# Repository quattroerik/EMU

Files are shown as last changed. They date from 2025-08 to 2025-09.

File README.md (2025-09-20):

[][cc-by-nc-sa]

# EMU – Expandable Multi-material Unit
### A new take on a MMU by <a href="https://github.com/DW-Tas">DW-Tas</a> and <a href="https://github.com/igiannakas">igiannakas</a><br/>
<a href="https://ko-fi.com/O5O5OCC0K"> Ko-Fi</a>

> [!WARNING] 
> ***Under Active/Early Development*** <br/>
> Build at your own risk

**Introducing the EMU, the Expandable Multi-material Unit from down under.** The EMU is a modular, flexible, upgradable, reliable and service-friendly MMU designed around the proven filamentalist V3 platform.

The EMU supports any number of lanes and base configurations; whether it is a **single lane setup** to assist filament loading, a **dual lane configuration** for endless spool, or a **multi-lane, multi base unit setup** for multi-material printing. It is also **expandable**, with no re-printing of parts required when upgrading from a 2 lane to a multiple lane setup.

<p align="center">
  
</p>

#### Table of Contents
- [Design Objectives & Key Features](#design-objectives)
- [BOM](#bom)
- [Assembly Videos](#assembly-videos)
- [Wiring Instructions and Diagrams](#wiring-diagrams)
- [Render Gallery](#render-gallery)
- [License](#this-work-is-licensed-under-a)

#### Highlights:
- **Modular & Expandable** design, able to add lanes anytime and in any configuration. No reprints when upgrading from a 2 lane setup.
- **One screw or tool-free** access and servicing, even mid-print.
- **Sealed dry boxes** able to maintain humidity in the 15% range (with silica gel) or 5–8% range (with molecular sieves) for weeks.  
- **Humidity** sensors per lane for environmental monitoring.
- **Reliable endless spool** with no chance of the rewound filament interfering with neighbouring rolls.
- **Off-the-shelf electronics** (EBB42 with EBB36 also fully compatible).  
- **Per-lane controls** - eject button + LEDs.

<p align="center">
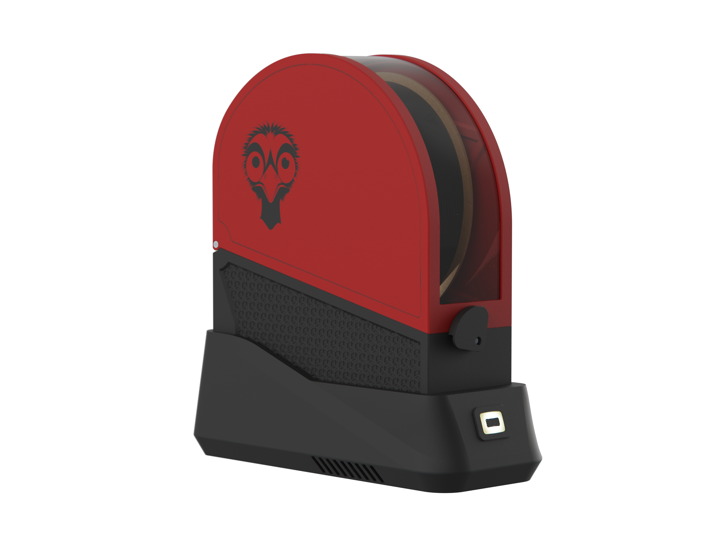
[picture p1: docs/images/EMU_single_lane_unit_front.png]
  
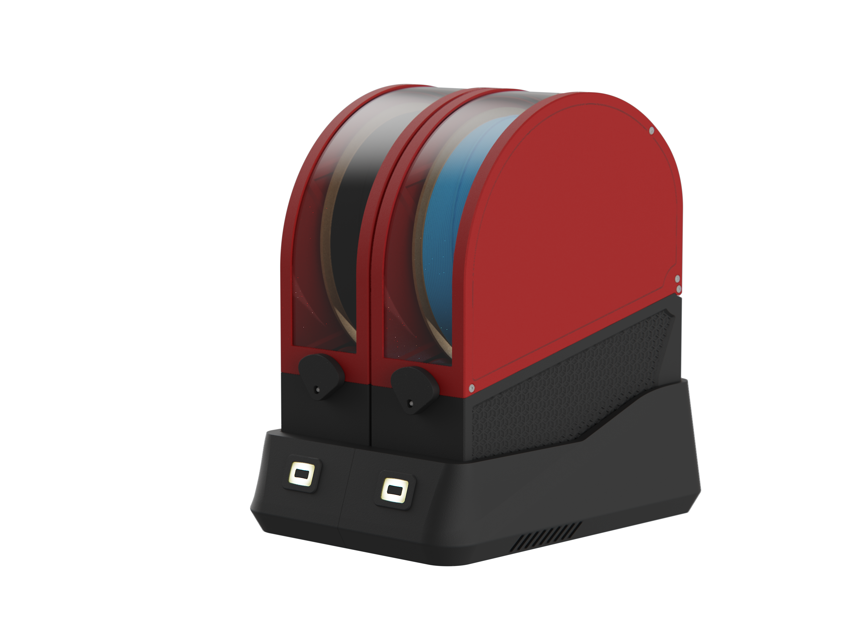
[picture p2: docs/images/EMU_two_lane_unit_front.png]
  
</p>

## Design Objectives

#### Modularity & Upgradeability  
Each lane is fully self-contained, so you can choose **exactly how many lanes you need and group them as you like**. You can also **mix and match** lanes across multiple base units, or use a stand-alone single lane for extruder loading and print assistance. 

Expanding later is also straightforward. Just print lane expanders for the base and add another dry box assembly. There is no need to reprint or replace existing parts when upgrading from a 2 lane base. 

#### Ease of Servicing 
All electrical and mechanical components are either **one screw or completely tool-free and immediately accessible**, making live troubleshooting possible even during a print. 

Access to the electronics is easy - just lift the dry box off its base for full access. The stepper tensioning screw is accessible without any dissassembly allowing on the fly tuning of filament grip. Finally, removing the filamentalist, stepper and stepper assembly is possible via one screw.

#### Sealed Dry Boxes  
Each spool sits in its own purpose built, **fully sealed dry box with an integrated desiccant holder**. The boxes use foam cord in areas of potential air ingress to create a tight seal, with the clear 1.5mm PETG/PC panel also offering visibility inside the dry box.

The dry boxes can maintain humidity in the 15% range (with silica gel) or 5–8% range (with molecular sieves) for weeks. Finally, as each dry box is self contained, opening one to reload filament, doesn’t disturb its neighbours, extending the effective desiccant life.

<p align="center">
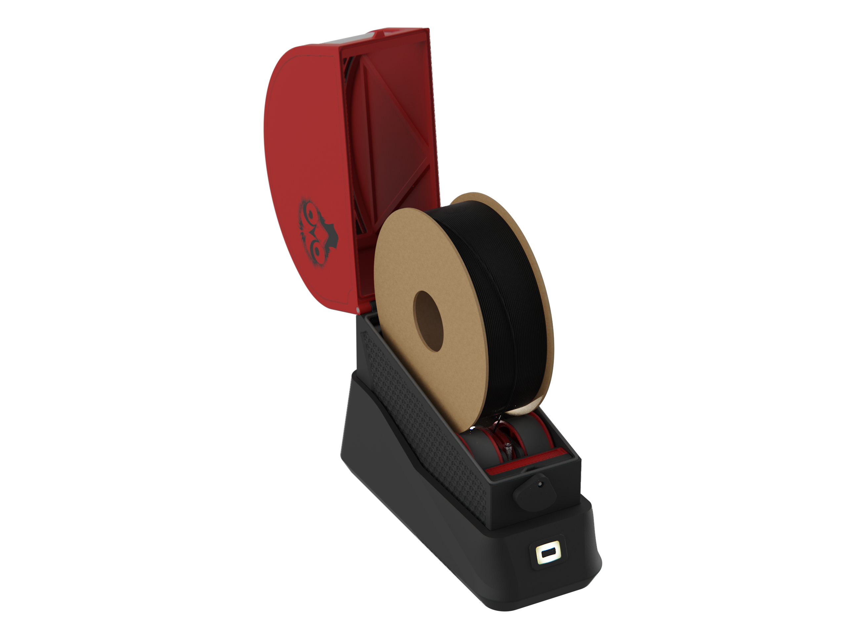
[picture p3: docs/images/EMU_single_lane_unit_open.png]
  
</p>

#### Integrated Humidity Sensors 
Each lane monitors its own environment, letting you know when it’s **time to refresh the desiccant**. The humidity sensors are integrated into Mainsail (and optionally in Home Assistant for historical data tracking via the mainsail HA integration).

#### Endless Spool Reliability
Dual pre-stepper sensors ensure **consistent run-out detection** and reliable re-wind, as the filament is always gripped by the stepper hobbed gear assembly. 

In addition, the isolated boxes ensure that any left over, rewound, filament cannot interfere with neighbouring lanes, **preventing a jam**.

#### Built on the Filamentalist
The lane assembly is based on the proven **[filamentalist V3 design with 688 bearings](https://github.com/Enraged-Rabbit-Community/ERCF_v2/tree/master/Recommended_Options/Filamentalist_Rewinder/Filamentalist_FV3_Rewinder)**, with no modifications necessary. 
- Existing 688 bearing version filamentalist parts can be reused when building an EMU.
- Optionally, the revised tensioner mount further improves pre-stepper switch actuation.
- Wide spool size compatibility - built on the 74mm filamentalist stock setup and fits even KVP filament spools.

<p align="center">
  
  
</p>

#### Integrated Filament Driving Stepper 
Each lane has its own driving stepper inside the dry box, resulting in a compact, **fully self-contained mechanical design**. In case of mechanical issue, you can swap out filamentalist assemblies with 3 screws, unplugging 2 JST plugs and unplugging the bowden tube. 

In addition, you can **swap out complete dry boxes** by unplugging two JST plugs and the bowden tube. This is helpful if you want to maintain a particularly moisture sensitive filament undisturbed when swapping it out from the EMU.

#### Simple Electronics
The recommended BOM uses **readily available EBB42 boards** (with EBB36 fully compatible). MMB v2 boards can also be reused, though without humidity sensing due to I²C limitations and a slightly more intricate wiring.

In addition, **each lane has its own ventilation fan**, ensuring the stepper drivers do not overheat, even when the unit is placed on top of a hot printer. With the EBB42 and EBB36, the ventilation fans can also be speed controlled to minimize noise.

#### Easy mounting
The EMU base assembly can be securely **mounted on extrusions** or using **rubber feet** directly on the printer or besides it. In either case the **electronics remain accessible** without needing to remove the unit from its mounts.

#### Per-lane Controls  
Each lane includes its own eject button, status LED, and a filament colour LED that illuminates the dry box. 

## BOM  
[Draft BOM here](https://docs.google.com/spreadsheets/d/1jYJXBgpc_iLDfC17fC2LTYKrSEy5ocPbGEQ_EEOGCvI)

## Assembly Videos

**Part 1: Filamentalist and Stepper Assembly Guide**<br/>
EMU Filamentalist and Stepper Assembly Guide (https://www.youtube.com/watch?v=FNcXC9HXUmI)
<br/>

**Part 2: Drybox Assembly Guide**<br/>
EMU Dry Box Assembly Guide (https://www.youtube.com/watch?v=JZzMyOBCdSM)
<br/>

**Part 3: Base Assembly Guide** <br/>
EMU Base Assembly Guide (https://www.youtube.com/watch?v=2SmAMuXas38)
<br/>

**Part 4: Electronics Assembly Guide** <br/>
EMU Elecrronics Assembly Guide (https://www.youtube.com/watch?v=Iang2JYkTh8)
<br/>

## Wiring Diagrams
Depending on the number of lanes assembled, the wiring will vary slightly. Below are some initial wiring key notes to get your started.<br/>

**Multi-lane setup wiring notes (2+ lanes)**
1. Please note that the sync feedback sensor is connected to the first lane board. The encoder and combiner endstop is connected to the second lane EBB board.
2. The CAN bus umbilical from the printer feeds power and the CAN H / L wires to the WAGO connectors in the first lane. 
3. A 24V and Ground "bus" is established throughout the base unit using the two rearward WAGO connectors (WAGO 3 and WAGO 4).
4. The EBB boards connect to the power bus for power via their XT ports.
5. The EBB boards are daisy chained to establish the CANbus network. The first lane canbus High / Low / Power wires are connected to the first lane WAGO connectors.
7. The second lane canbus High / Low wires are connected to the CAN out dupont connectors on the first board itself. Creates the daisy chain
9. The last EBB board needs the 120Ohm resistor installed.
10. The second lane, third lane etc 2nd WAGO connector is used to connect the Neopixel Out wire from the eject button to the Neopixel In wire on the dry box.
11. The second lane, third lane etc 1st WAGO connector is used to connect the Neopixel Out wire from the dry box to the next lane Neopixel In wire on the eject button.

**Adding a second base unit** <br/>
You can daisy chain as many base units as you desire. Simply wire the XT30+2 CAN out port next to the last lane to the power bus and CAN H / L dupont connectors on the last EBB board. The next base unit can connect using a standard CAN Bus cable to the first unit.

**Single-lane setup wiring notes (2+ lanes)** <br/>
1. A single lane setup does not support an encoder/combiner. Instead, the Post Extruder sensor is configured in the Happy Hare configuration as the gate sensor.
2. There is no daisy chaining required. The single EBB board is connected to the first lane WAGO connectors.
3. There is no daisy chaining of subsequent lane Neopixels. 

**EBB 42 wiring diagram**<br/>
<p align="center">
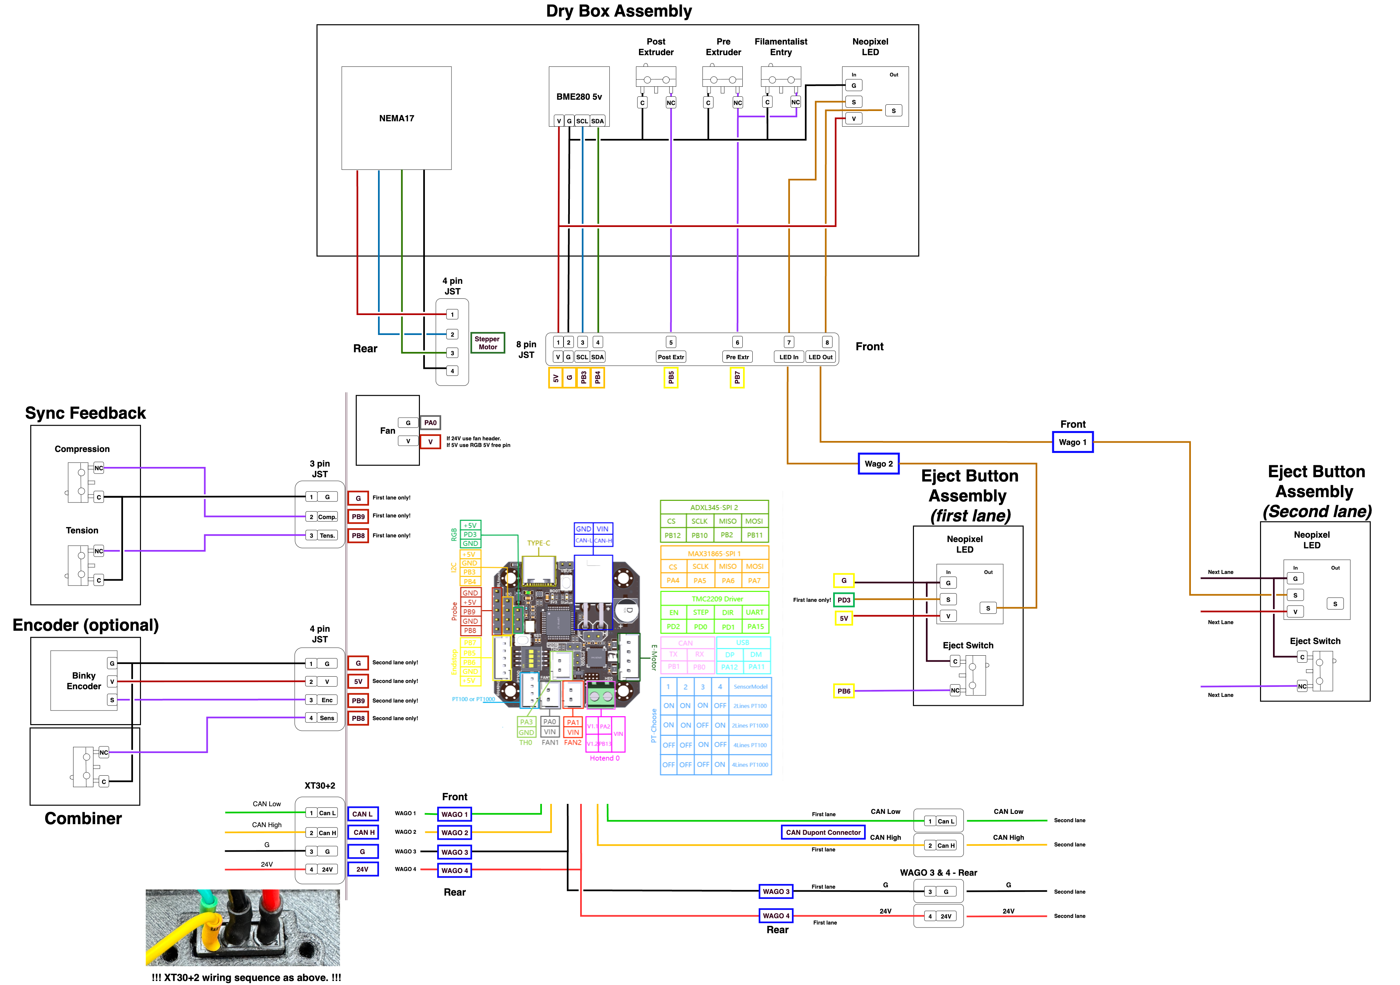
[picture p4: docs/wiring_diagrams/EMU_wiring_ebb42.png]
  
</p>

**EBB 36 wiring diagram**<br/>
Please note, the EBB36 uses identical pin definitions to the EBB42.
<p align="center">
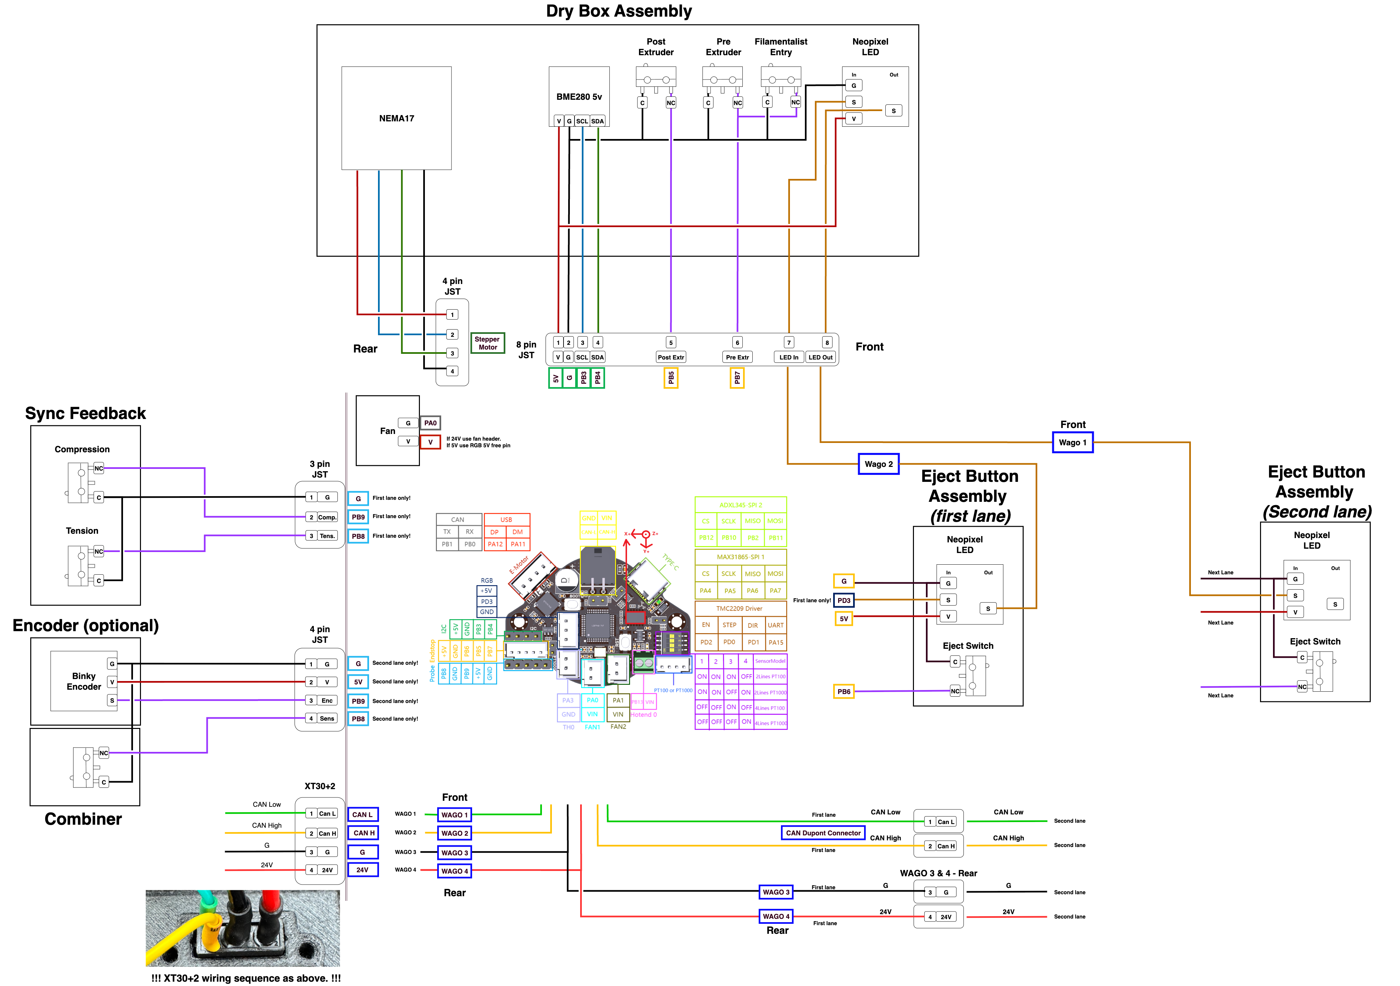
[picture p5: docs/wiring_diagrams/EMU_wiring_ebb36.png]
  
</p>

**Printer PSU**<br/>
> [!WARNING]
> You need to evaluate whether your PSU has enough power headroom to operate the number of lanes of your choosing. This entirely depends on your printer's overall setup and how many lanes of the EMU you are planning to build.

Key factors to consider:
1. PSU wattage
2. How many A-B/X-Y and Z steppers 
3. At what current the main printer steppers are operating at 
4. Your heater cartridge wattage 
5. What other power consuming accessories are connected to the printer (cpap, heater bed if 24V etc)
6. How many EMU lanes you are planning to build

Depending on the combined power consumption, you may need to consider whether a PSU upgrade is needed. 

As a rule of thumb, a 12 lane EMU build with 4 Z steppers and 2 AB steppers running moderately high currents and high print speeds on a Voron 2.4 may require a 350Watt power supply to ensure adequate power headroom.

### Render Gallery
<p align="center">
  
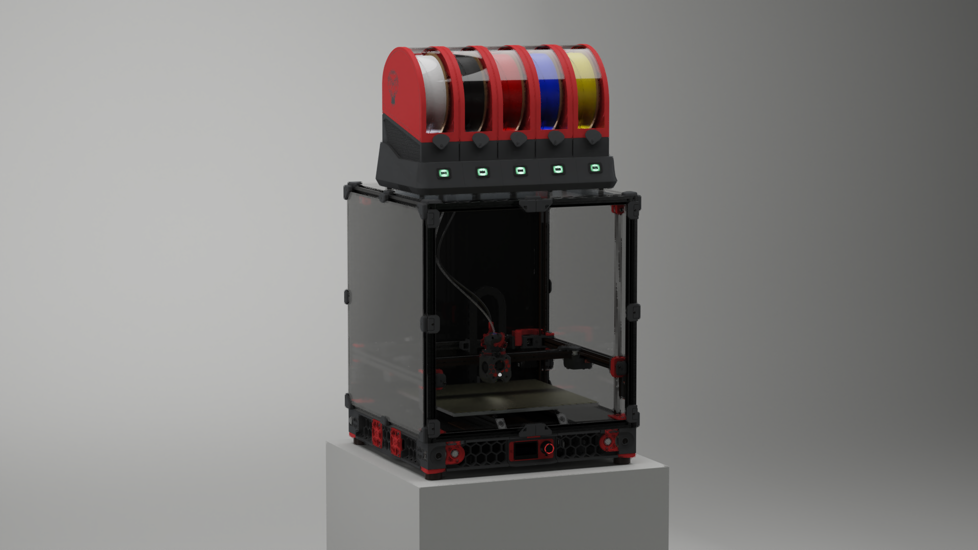
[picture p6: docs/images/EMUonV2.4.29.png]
  
</p>
<p align="center">
  
  
</p>
<br/>

#### This work is licensed under a
[Creative Commons Attribution-NonCommercial-ShareAlike 4.0 International License][cc-by-nc-sa].

[][cc-by-nc-sa]

[cc-by-nc-sa]: http://creativecommons.org/licenses/by-nc-sa/4.0/
[cc-by-nc-sa-image]: https://licensebuttons.net/l/by-nc-sa/4.0/88x31.png
[cc-by-nc-sa-shield]: https://img.shields.io/badge/License-CC%20BY--NC--SA%204.0-lightgrey.svg

### License clarification regarding non-commercial use:
The non-commercial aspect of this license is for cases where EMU is the product, not the use of EMU to create products.<br/>
I.e. If you wish to sell EMU as a product, you would need to seek a commercial license before doing so. </br>
It is NOT intended to prevent the use of EMU with a printer that you use to provide commercial services. If you want to run EMU in your print farm, go right ahead.

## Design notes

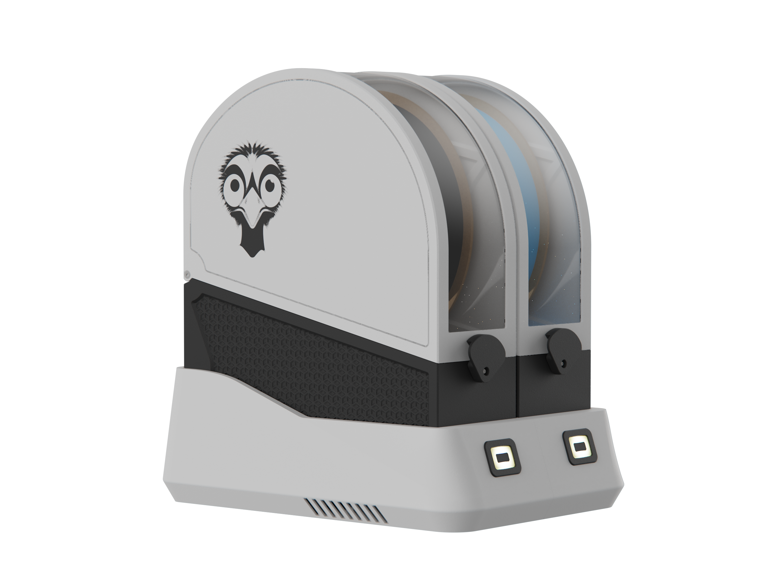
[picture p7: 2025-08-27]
docs/images/EMU_two_lane_unit_white.png

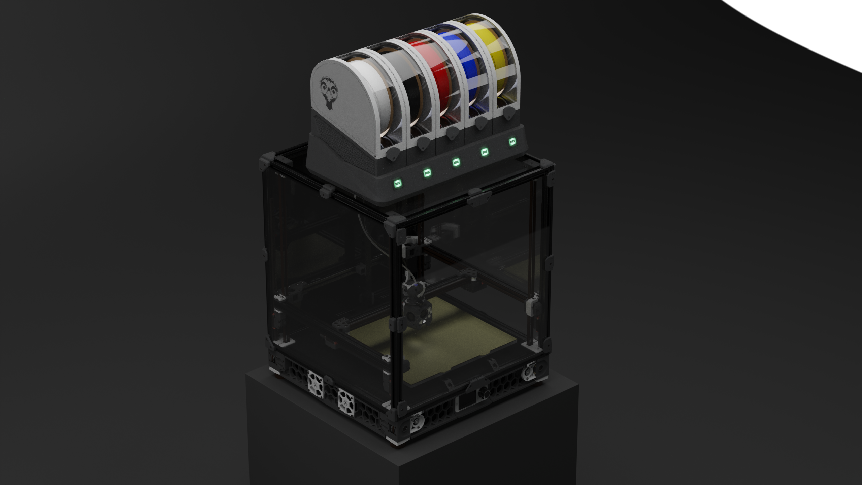
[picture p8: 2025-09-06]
docs/images/EMUonV2.34.png

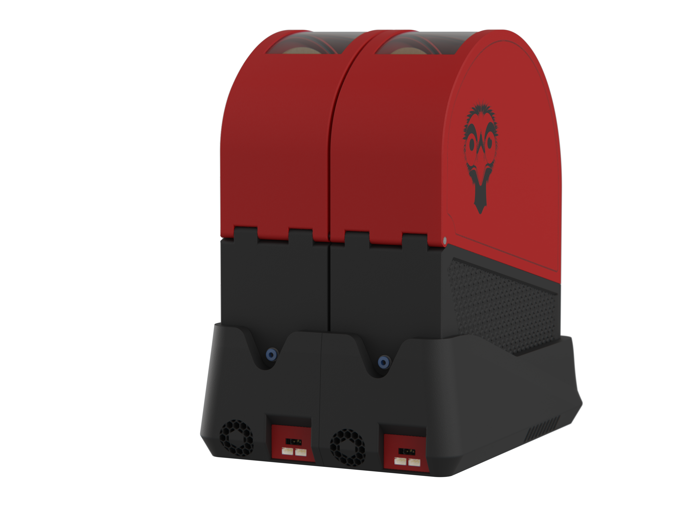
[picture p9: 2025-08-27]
docs/images/EMU_two_lane_unit_rear.png

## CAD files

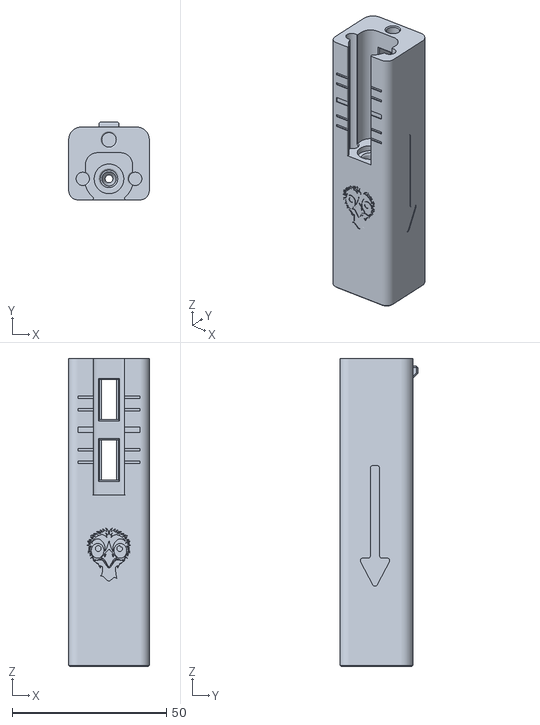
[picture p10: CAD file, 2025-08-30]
STL/Tension-compression-sensor/EMUSync_main_body.stl
26.1 x 25.2 x 99.8

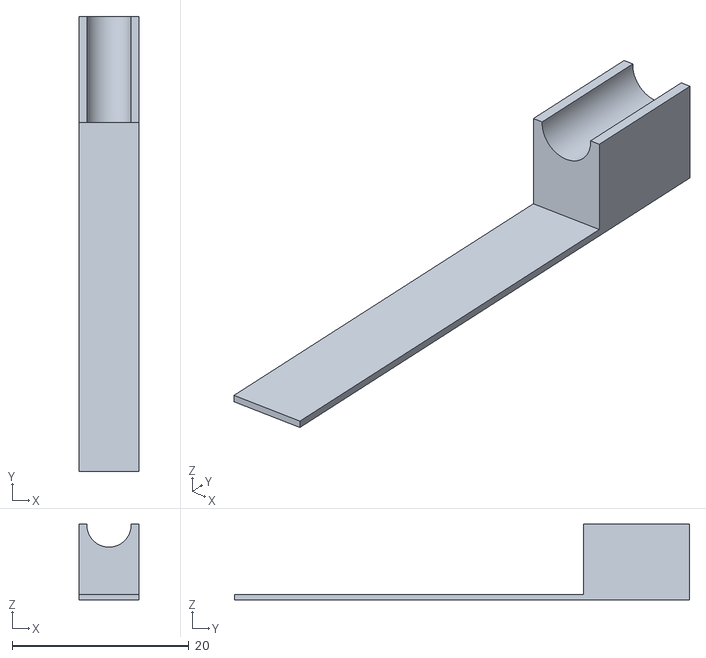
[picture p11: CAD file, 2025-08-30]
STL/Tension-compression-sensor/EMUSync trigger assembly installation tool.stl
6.80 x 51.5 x 8.60

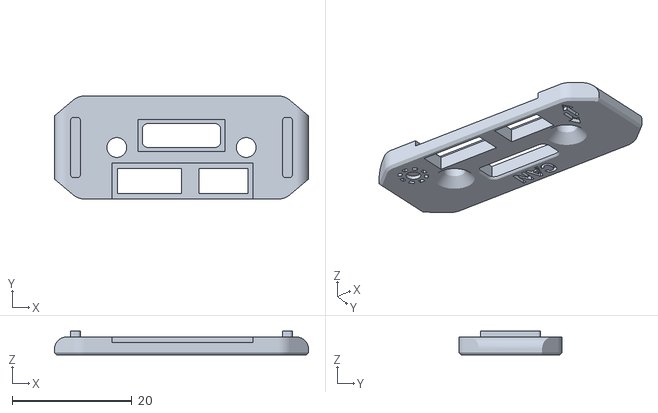
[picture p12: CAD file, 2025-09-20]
STL/Base/[a]_Cable_Entry-Inside_x2.stl
42.4 x 17.2 x 4.00

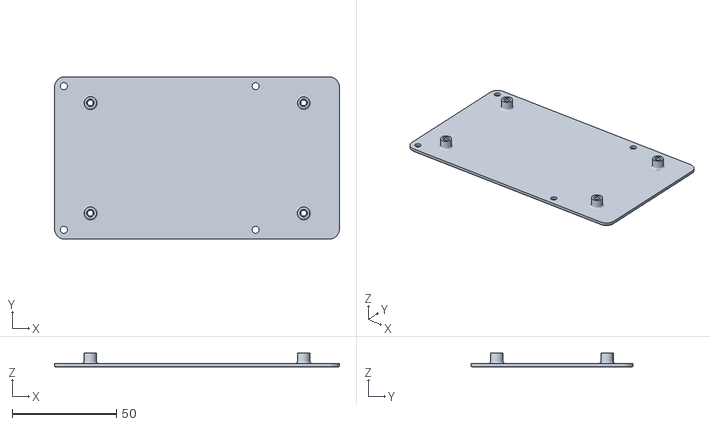
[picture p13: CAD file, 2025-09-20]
STL/Base/Optional/[a]_MMBv2_mount[boo_stinky_4lane].stl
137.0 x 78.0 x 6.80

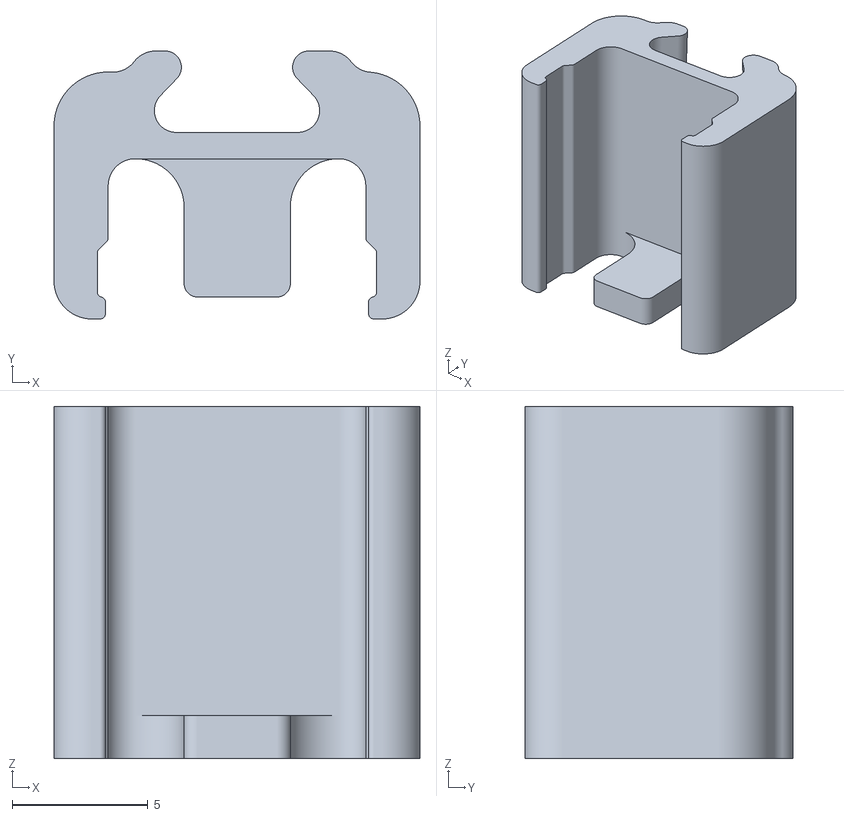
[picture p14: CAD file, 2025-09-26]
STL/Box/[a]_BME280_Holder[+1mm].stl
13.5 x 9.88 x 13.0

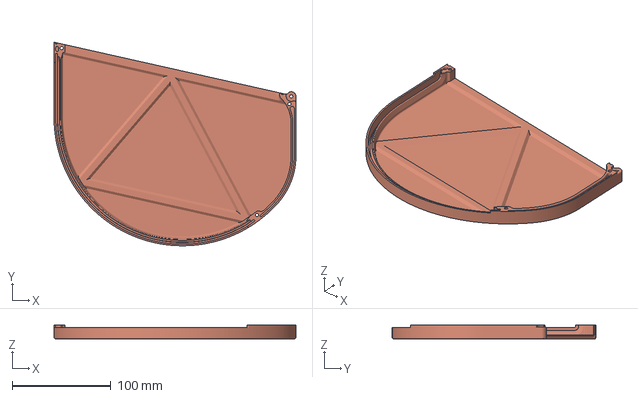
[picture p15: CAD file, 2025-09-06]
STL/Box/Lid MMU/[a]_Box_Lid_right_mmu.3mf
245.0 x 206.1 x 13.9 mm
[a]_Box_Lid_right_mmu
border_inset

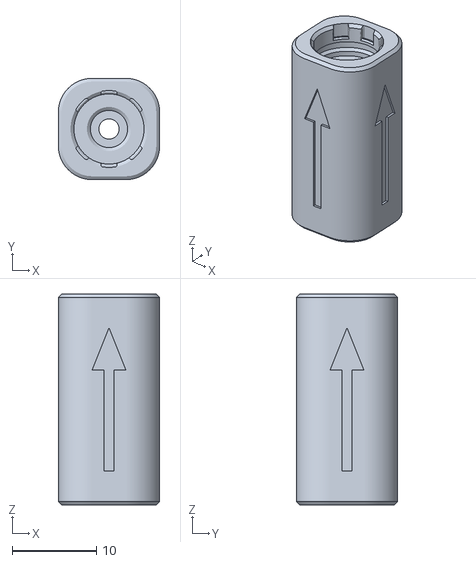
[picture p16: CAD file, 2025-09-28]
STL/Combiner-encoder/Combiners_no_sensor/Combiner_1-1.stl
12.0 x 12.0 x 25.0

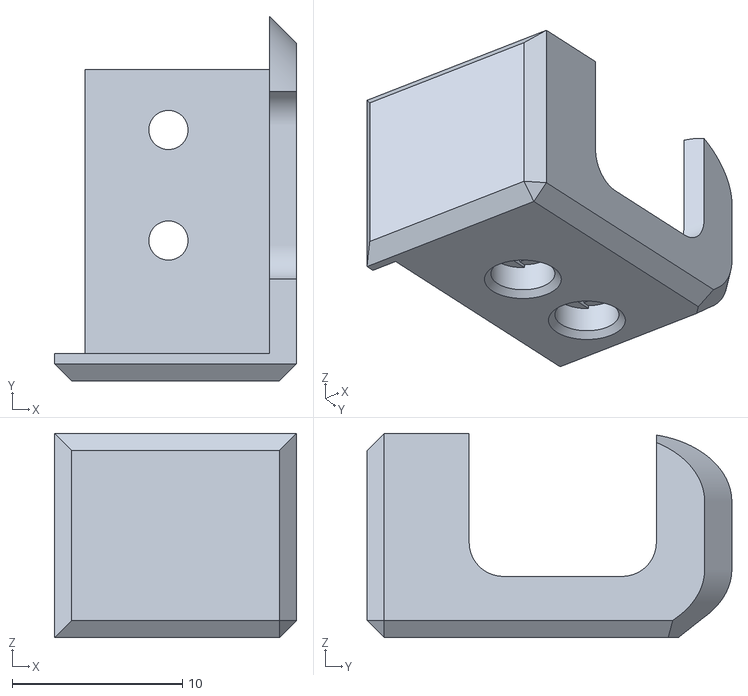
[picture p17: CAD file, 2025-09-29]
STL/Combiner-encoder/Combiners_with_sensor/[a]Combiner_sensor_cap.stl
14.2 x 21.4 x 12.0

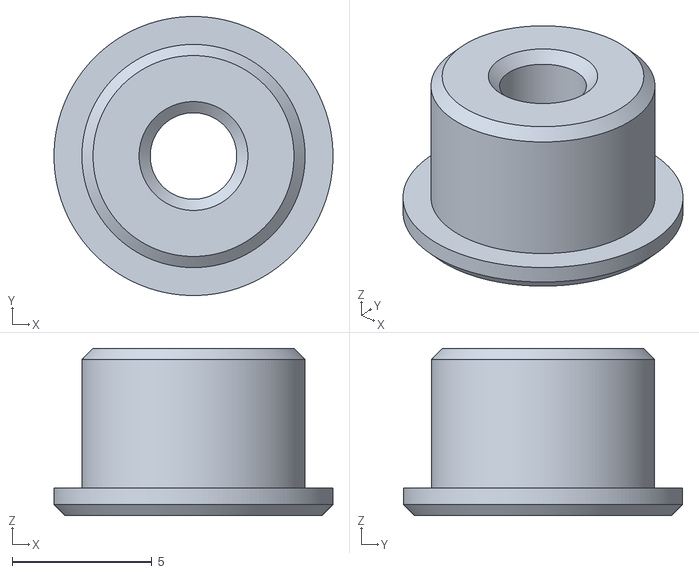
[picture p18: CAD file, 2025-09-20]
STL/Combiner-encoder/Encoder_no_sensor/688_Bushing.stl
10.0 x 10.0 x 6.00

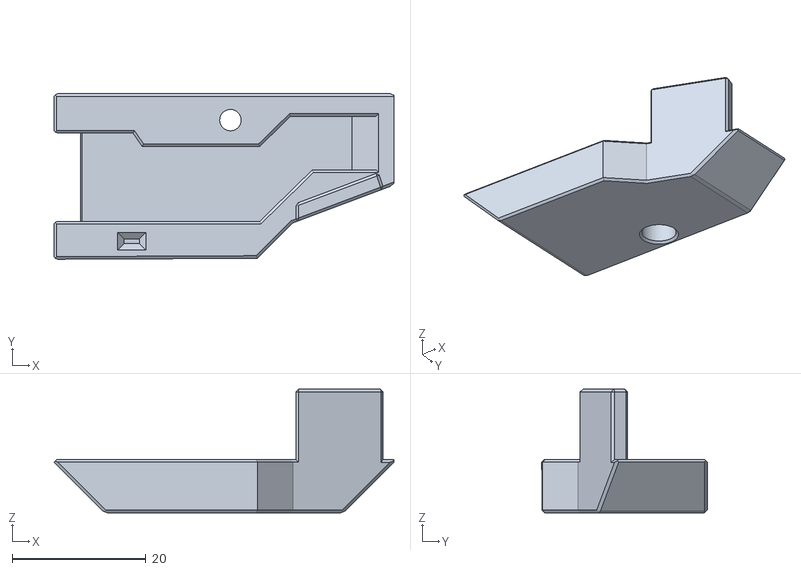
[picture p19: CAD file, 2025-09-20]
STL/Combiner-encoder/Encoder_with_sensor/[a]_Encoder_Top.stl
50.9 x 24.8 x 18.5

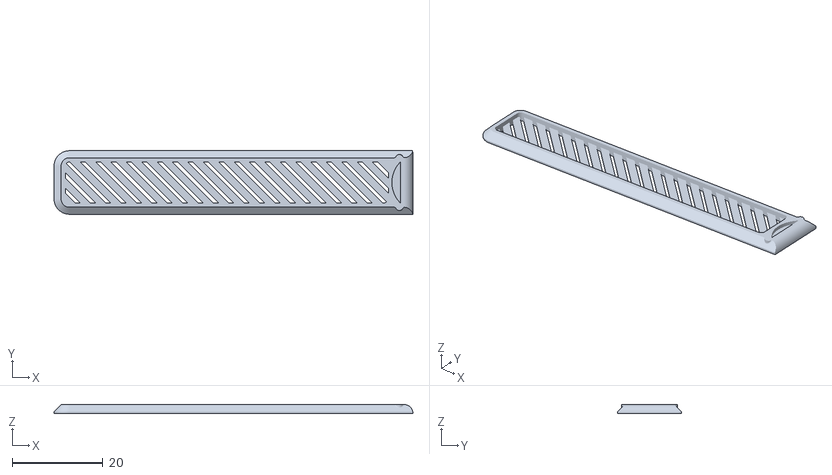
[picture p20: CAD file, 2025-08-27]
STL/Desiccant-box/[a]_Desiccant_Box_Lid.stl
79.2 x 14.0 x 2.00

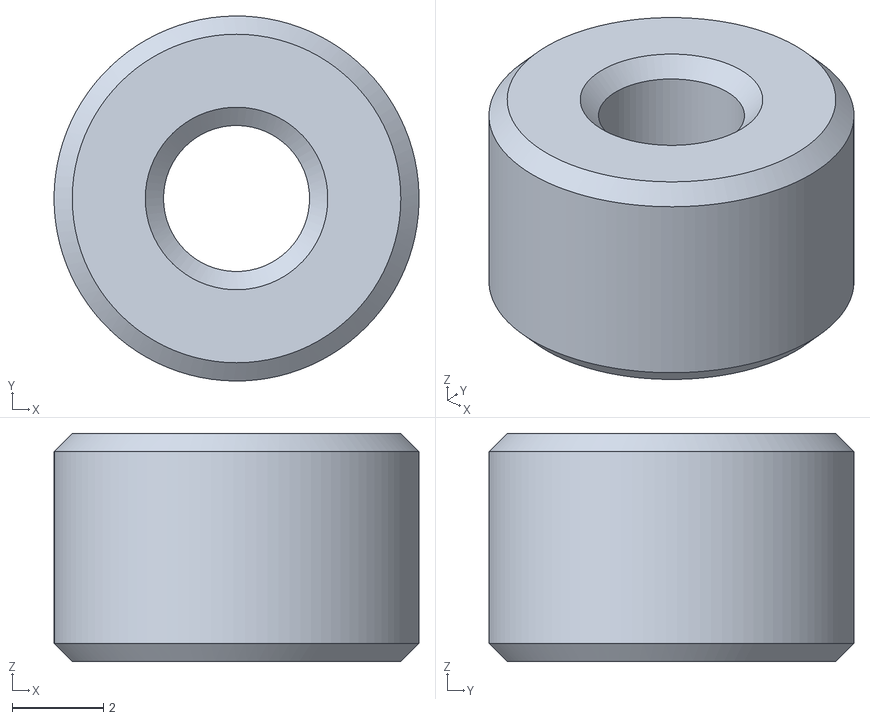
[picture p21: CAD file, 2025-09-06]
STL/Filamentalist/688_Bearing_Bushing.stl
8.00 x 8.00 x 5.00

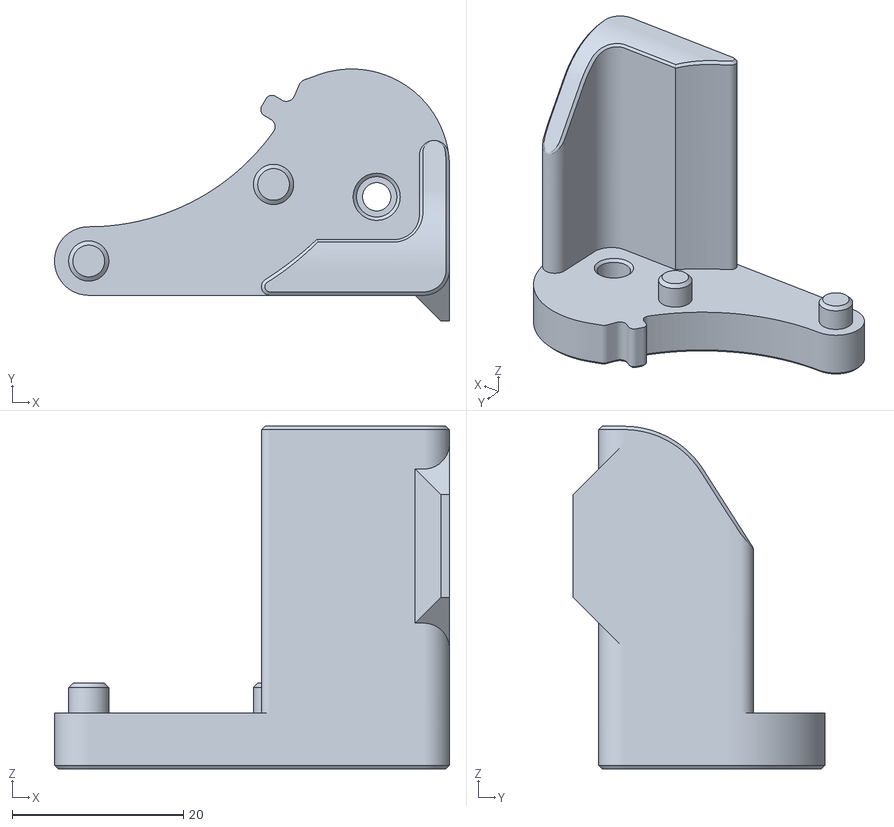
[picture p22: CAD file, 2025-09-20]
STL/Stepper/Box_Mnt_Front_L.stl
46.1 x 29.4 x 40.0

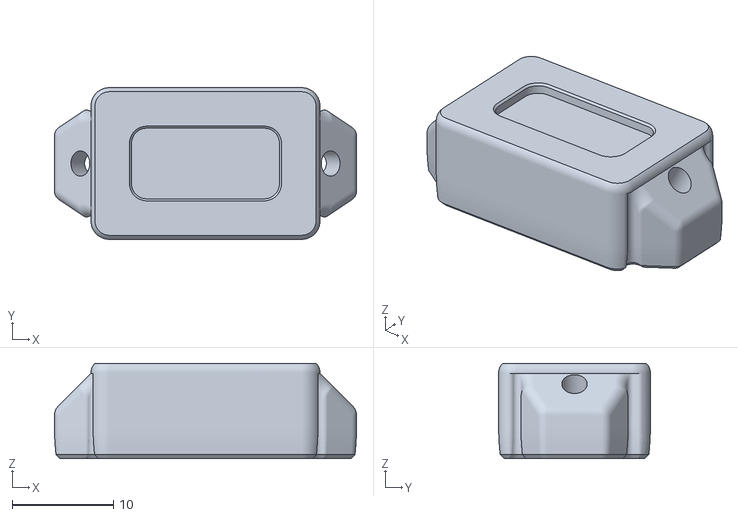
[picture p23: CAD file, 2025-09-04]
STL/Base/[t]_Button_Diffuser.stl
29.8 x 15.0 x 9.40

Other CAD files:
STL/Box/[a]_Box_Lid_right.stl
STL/Combiner-encoder/Encoder_no_sensor/12_Tooth_Encoder_Slotted_Wheel.stl
STL/Combiner-encoder/Encoder_with_sensor/Encoder_Left.stl
STL/Desiccant-box/Desiccant_Box_Base.stl
STL/Base/Button_Filter.stl
STL/Base/Button_Rear.stl
STL/Base/[a]_Cable_Entry-Outside_x2.stl
STL/Base/[a]_Ebb36_Mount.stl
STL/Base/[a]_Ebb42_Mount.stl
STL/Base/[a]_Wago221-413_Holder.stl
STL/Base/[t]_Button_Diffuser[thicker_PCB].stl
STL/Box/Box_Latch.stl
STL/Box/[a]_BME280_Holder.stl
STL/Box/[a]_Box_wiring_hatch.stl
STL/Combiner-encoder/Encoder_no_sensor/Encoder_Left.stl
STL/Combiner-encoder/Encoder_no_sensor/[a]_Encoder_Top.stl
STL/Combiner-encoder/Encoder_with_sensor/12_Tooth_Encoder_Slotted_Wheel.stl
STL/Filamentalist/Chassis_L_688_Bearing.stl
STL/Filamentalist/Chassis_R_688_Bearing.stl
STL/Filamentalist/EMU_Tensioner_Mount_with_Sensor.stl
STL/Filamentalist/Idler_Roller_Axle.stl
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

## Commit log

2025-08-27 Upload STLs
    [12_Tooth_Encoder_Slotted_Wheel.stl, 688_Bushing.stl, Box_Latch.stl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]
2025-08-27 cableway entry cover STLs
    [[a]_Cable_Entry-Inside_x2.stl, [a]_Cable_Entry-Outside_x2.stl]
2025-08-27 fix name of stepper parts
    [Box_Mnt_Front_L.stl, Box_Mnt_Front_R.stl, Idler_Roller_Axle.stl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]
2025-08-28 BOM and Assembly video sections
2025-08-29 very minor printability fix for box_base.stl (not a reprint)
2025-08-29 moved environment sensor mount inside box base for easier reach to install.
2025-08-29 Updated filamentalist assembly video with updated bowden tube dimensions
2025-08-30 EMUSync STLs
    [EMUSync PTFE Cutter and Length Tool.stl, EMUSync trigger assembly installation tool.stl, EMUSync_main_body.stl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]
2025-08-30 Additional button diffuser for LEDs with thicker PCB material
    [[t]_Button_Diffuser[thicker_PCB].stl]
2025-08-30 fix oversized holes in EBB mounts
    [[a]_Ebb36_Mount.stl, [a]_Ebb42_Mount.stl]
2025-08-31 Readme updates with part 2 assembly guide and link to Filamentalist V3 688 repo.
2025-08-31 added markings to cable entry covers to help identify connections
    [[a]_Cable_Entry-Inside_x2.stl, [a]_Cable_Entry-Outside_x2.stl]
2025-08-31 Increase tolerances around magnets and switch for front button to make them easier to install.
    [Button_Rear.stl, [t]_Button_Diffuser.stl, [t]_Button_Diffuser[thicker_PCB].stl]
2025-08-31 change cable intry covers to accept a different JST plug for encoder. And Wago holder to accept 8mm BHCS
    [[a]_Cable_Entry-Inside_x2.stl, [a]_Cable_Entry-Outside_x2.stl, [a]_Wago221-413_Holder.stl]
2025-08-31 allow for JST sockets to be inserted either way.
    [[a]_Box_wiring_hatch.stl]
2025-08-31 Minor printability fix for base sections to improve a bridge above the button.
2025-09-01 Readme update with aggregated per lane BOM
2025-09-04 reinforced front of lid, updated button for magnet tolerences
    [Button_Rear.stl, [a]_Box_Lid_right.stl, [a]_Box_Lid_right_mmu.3mf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]
2025-09-06 added 688 bearing buhsing STL for filamentalist
    [688_Bearing_Bushing.stl]
2025-09-06 Upload wiring diagrams
2025-09-06 Initial wiring instructions and diagrams added
2025-09-06 Single lane setup wiring notes. Adding a second base unit wiring notes.
2025-09-06 upload higher resolution STL/3MF parts for box and base
    [[a]_Box_Lid_right_mmu.3mf]
2025-09-06 Uploaded base assembly guide video
2025-09-08 increase screw hole tolerance in 688 bushing for encoder
    [688_Bushing.stl, Encoder_Left.stl]
2025-09-09 New combiners and update stepper main body for better reach of square nut for tension arm and replace the only M3x25 screw for M3x20
2025-09-13 Wiring diagram updates
2025-09-13 Wiring video upload
2025-09-14 updated to fix screw hole clearance before heatset - Box_Mnt_Front_L.stl
    [Box_Mnt_Front_L.stl]
2025-09-14 Wiring diagram file rename.
2025-09-15 Updated Part 1 Filamentalist and Stepper assembly video to remove M3x25 screw and replace with M3x20 as per CAD changes.
2025-09-18 Fixes to sensor switch placement and ECAS fittings
    [12_Tooth_Encoder_Slotted_Wheel.stl, 688_Bushing.stl, Combiner_sensor_cap.stl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]
2025-09-18 rename accent part STL (combiner cap)
    [[a]Combiner_sensor_cap.stl]
2025-09-18 mmb optional mounting bracket
    [[a]_MMBv2_mount[boo_stinky_4lane].stl]
2025-09-18 cable entry cover - inside fix tolerance to JST plug
    [[a]_Cable_Entry-Inside_x2.stl]
2025-09-20 Upload button diffuser mmu file with lane numbering (thicker PCB variant)
2025-09-26 minor part changes for screw head clearance and wider slot on BME holder
    [[a]_BME280_Holder[+1mm].stl]
2025-09-28 Update for combiners with sensor to remove snag post sensor
    [Combiner_1-1.stl, [a]Combiner_sensor_cap.stl]
2025-09-29 moved swtich screw position towards filament path in combiner+sensor parts
    [[a]Combiner_sensor_cap.stl]
2025-09-29 Deprecated bushing on roler bearing tension arm: [a]_Stepper_Tension_Arm[bushing].stl
    [[a]_Stepper_Tension_Arm[bushing].stl]
2025-09-29 increased clearance around tension screw in stepper main body
2025-10-19 Updated lower box with new wire hatch / Added heatset inserts to base
2025-10-21 Added mounting point for BME board to under side of LED_holder to make mounting and wiring easier.

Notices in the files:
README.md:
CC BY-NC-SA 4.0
